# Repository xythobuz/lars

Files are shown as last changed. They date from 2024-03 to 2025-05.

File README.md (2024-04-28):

# LARS - Looping Automated Rhythm Station






This is a simple drum machine / loopstation.
It's made for three hand-wound solenoids mounted to a tambourine.
It is controlled by a Raspberry Pi Pico on a custom PCB.

Please take a look at [the auto-generated documentation](https://xythobuz.github.io/lars/).

Also see [this blog post for some more context](https://www.xythobuz.de/lars.html).

## Quick Start

Initialize your local repo and prepare the build:

    git clone https://git.xythobuz.de/thomas/drumkit.git
    cd drumkit
    git submodule update --init
    cd pico-sdk
    git submodule update --init
    cd ..
    mkdir build
    cd build
    cmake ..
    cd ..

Then you can build new binaries like this:

    make -Cbuild -j4

For the first time, flash as usual using the mass storage bootloader (hold BOOTSEL while pluggin in the Pico).
After the firmware has been flashed once you can just use the included `flash.sh` to avoid having to hold the button.
Use `debug.sh` to open a serial console via USB.

## Documentation

You can find the [documentation here on GitHub pages](https://xythobuz.github.io/lars/).

The docs are built using [mdbook](https://github.com/rust-lang/mdBook), licensed as `MPL-2.0`.
Get the [latest release from GitHub](https://github.com/rust-lang/mdBook/releases) for a pre-built binary if you want to test changes to the docs locally.

    ./pcb/generate_plot.sh
    ./pcb2/generate_plot.sh
    ./3dprint/generate_stls.sh

    ./docs/generate_docs.sh serve

This will open your browser to a local development instance of the docs.

## Hardware Connections

These are the used pins on the first prototype.
Follow these if you want to build your own version without the included PCB design.

    Pin 1    GP0    I2C0 SDA
    Pin 2    GP1    I2C0 SCL

    Pin 29   GP22   Output Channel A
    Pin 31   GP26   Output Channel B
    Pin 32   GP27   Output Channel C

    Pin 34   GP28   Vbat (ADC2)

    Pin 11   GP8    Button 1
    Pin 12   GP9    Button 2
    Pin 16   GP12   Button 3
    Pin 19   GP14   Button 4

    Pin 22   GP17   Encoder A
    Pin 24   GP18   Encoder B
    Pin 21   GP16   Encoder Click

    Pin 14   GP10   LED 1
    Pin 15   GP11   LED 2
    Pin 17   GP13   LED 3
    Pin 20   GP15   LED 4

## License

The firmware of this project is licensed as GPLv3.
A copy of the license can be found in `COPYING`.

It uses the [Pi Pico SDK](https://github.com/raspberrypi/pico-sdk), licensed as BSD 3-clause, and therefore also [TinyUSB](https://github.com/hathach/tinyusb), licensed under the MIT license.

Some code is adapted from the TinyUSB examples.

To control the OLED display, [pico-ssd1306](https://github.com/daschr/pico-ssd1306) is used, licensed under the MIT license.

The code in `src/encoder.c` is derived from [mathertel/RotaryEncoder](https://github.com/mathertel/RotaryEncoder) and therefore licensed as BSD 3-clause.

Repo metadata is embedded into the project using [cmake-git-version-tracking](https://github.com/andrew-hardin/cmake-git-version-tracking), licensed under the MIT license.

The docs are built using [mdbook](https://github.com/rust-lang/mdBook), licensed as `MPL-2.0`.

The PCB SVG files in the documentation are displayed using [svg-pan-zoom](https://github.com/bumbu/svg-pan-zoom), licensed as `BSD-2-Clause`.

The 3D PCB files in the documentation are displayed using [three.js](hhttps://github.com/mrdoob/three.js), licensed as `MIT`.

Some code in `docs/src/js/3d.js` is derived from [a blog post of Michal Jirků](https://wejn.org/2020/12/cracking-the-threejs-object-fitting-nut/).

    This program is free software: you can redistribute it and/or modify
    it under the terms of the GNU General Public License as published by
    the Free Software Foundation, either version 3 of the License, or
    (at your option) any later version.

    This program is distributed in the hope that it will be useful,
    but WITHOUT ANY WARRANTY; without even the implied warranty of
    MERCHANTABILITY or FITNESS FOR A PARTICULAR PURPOSE.  See the
    GNU General Public License for more details.

    See <http://www.gnu.org/licenses/>.

The schematic and PCB design of this project is licensed under the [CERN Open Hardware Licence Version 2 - Strongly Reciprocal (CERN-OHL-S-2.0+)](https://ohwr.org/cern_ohl_s_v2.txt) or any later version.
A copy of the license can be found in `LICENSE`.

The PCB designs use a [KiCad-RP-Pico based](https://github.com/ncarandini/KiCad-RP-Pico) symbol and footprint library, licensed as `CC-BY-SA 4.0`.

The `pcb2/extern/EC12E-200.STEP` 3D model for the rotary encoder comes directly from the manufacturer, [ALPS](https://tech.alpsalpine.com/e/products/detail/EC12E24204A8/).

The `pcb2/extern/OLED_128x64.stp` 3D model for the SSD1306 OLED display is made by [
Adrián San José Torices](https://grabcad.com/library/pantalla-oled-0-96-128x64-1).

The SSD1306 footprint for pcb2 is from [KiCAD Rookie](https://kicadrookie.blogspot.com/2022/06/ssd1306-i2c-096in-oled-display-kicad_86.html).

The `pcb2/extern/5236AB/5236ab-41x408.stp` 3D model for the power switch comes directly from the manufacturer, [APEM](https://www.apem.com/idec-apem/de/Schalter-f%C3%BCr-Frontplatten/5000M/p/5236AB).

     ------------------------------------------------------------------------------
    | This source describes Open Hardware and is licensed under the CERN-OHL-S v2  |
    | or any later version.                                                        |
    |                                                                              |
    | You may redistribute and modify this source and make products using it under |
    | the terms of the CERN-OHL-S v2 (https://ohwr.org/cern_ohl_s_v2.txt)          |
    | or any later version.                                                        |
    |                                                                              |
    | This source is distributed WITHOUT ANY EXPRESS OR IMPLIED WARRANTY,          |
    | INCLUDING OF MERCHANTABILITY, SATISFACTORY QUALITY AND FITNESS FOR A         |
    | PARTICULAR PURPOSE. Please see the CERN-OHL-S v2 (or any later version)      |
    | for applicable conditions.                                                   |
    |                                                                              |
    | Source location: https://git.xythobuz.de/thomas/drumkit                      |
    |                                                                              |
    | As per CERN-OHL-S v2 section 4, should You produce hardware based on this    |
    | source, You must where practicable maintain the Source Location visible      |
    | on the external case of the Gizmo or other products you make using this      |
    | source.                                                                      |
     ------------------------------------------------------------------------------

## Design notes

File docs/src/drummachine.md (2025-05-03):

# Drum Machine

The drum-machine runs through a sequence of a given length, set by the `Length` menu.

The corresponding LED lights up at it's moment in the sequence.
The currently active "step" is fully bright while enabled ones are lit dimly.

Change the speed the sequence is running at with the `BPM` setting.

If you have selected a `Length` that is longer than the available number of buttons / LEDs, you can switch your "window" of the sequence using the `Bank` setting.

Select the currently edited output channel with the `Channel` menu.

Use the CLEAR button below the encoder to zero-out the currently selected channel.

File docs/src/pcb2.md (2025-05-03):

# LARS V2

This is the second iteration of the hardware.
The principle is the same as for the prototype, with the same chinese modules used.
Only the buttons have been changed, and there are now 9 of them, with 8 LEDs.
The battery is now mounted on the board.
It is planned to be used without a case.

You can [download the Gerber files to order PCBs online](./plot/fab_pcb2.zip).

assembled V2 PCB (https://www.xythobuz.de/img/lars_v2_1.jpg)

Revision 1 was using the SMD-only footprint for the Raspberry Pi Pico.
Revision 2 has changed this to be compatible to THT as well.

**Warning:**
Revision 1 and 2 are missing diodes on the button matrix.
So when holding down three or more buttons simultaneously you get ghosting on other buttons.

Depending on the solenoids you may reach a situation where not all channels can be properly triggered simultaneously.

**To Do**: try to improve this by adding more capacitance to the power rail or between the voltage regulators and the mosfets?

## Bill of Materials

These are all the parts required to assemble the V2 PCB.

| ID | Type | Link |
| -- | ---- | ---- |
| U1 | Raspberry Pi Pico | [Reichelt.de](https://www.reichelt.de/raspberry-pi-pico-rp2040-cortex-m0-microusb-rasp-pi-pico-p295706.html?&nbc=1), [Amazon.de](https://www.amazon.de/Raspberry-Pi-Pico/dp/B09KVB8LVR) |
| U2 | TP4056 Charger Module | [Amazon.de](https://www.amazon.de/AZDelivery-%E2%AD%90%E2%AD%90%E2%AD%90%E2%AD%90%E2%AD%90-TP4056-Laderegler-Lithium/dp/B07D2G345P) |
| U3 - U5 | MOSFET Module N-Channel | [Amazon.de](https://www.amazon.de/Schaltersteuerplatine-Motorsteuerplatine-MOSFET-Triggerschalter-Reglersteuerplatine-Dual-Hochleistungs/dp/B0CBK7D1GD) |
| U6 - U8 | Step-Up Converter Module | [Amazon.de](https://www.amazon.de/Converter-Spannungswandler-LAOMAO-Netzteil-Kompatibel/dp/B0B932BR7V) |
| OLED1 | SSD1306 128x64 0.96" Display | [Amazon.de](https://www.amazon.de/AZDelivery-Display-Arduino-Raspberry-gratis/dp/B01L9GC470) |
| BT1 | Keystone 1042 | [Reichelt.de](https://www.reichelt.de/batteriehalter-fuer-1-18650-keystone-1042-p213369.html?&nbc=1) |
| S1 | APEM 5236AB | [Reichelt.de](https://www.reichelt.de/kippschalter-1a-250vac-1x-ein-ein-printanschluss-as-500apc-p4396.html?&nbc=1) |
| SW1 | ALPS EC12E24244 | [Reichelt.de](https://www.reichelt.de/drehimpulsegeber-24-impulse-24-rastungen-vertikal-stec12e08-p73923.html?&nbc=1) |
| - | Cap for encoder knob | [Reichelt.de](https://www.reichelt.de/potentiometerknopf-fuer-achse-6-4-5-mm-schwarz-knopf-10-150e-p73960.html) |
| SW2 - SW10 | DIP 6x6mm push button | [Reichelt.de](https://www.reichelt.de/kurzhubtaster-printmontage-1-schliesser-6-x-6-x-5-mm-dip-dts-62k-v-p360043.html?&nbc=1) |
| D1 - D4 | 1N5819 Schottky Diode | [Reichelt.de](https://www.reichelt.de/schottkydiode-40-v-1-a-do-41-1n-5819-p41850.html?&nbc=1) |
| D5 - D12 | LED 5mm | [Reichelt.de](https://www.reichelt.de/led-5mm-bedrahtet-rot-450-mcd-90--5603r1c-khb-a-p361958.html?&nbc=1) |
| R1 | Resistor 10k Ohm 0.1% Axial | [Reichelt.de](https://www.reichelt.de/widerstand-metallschicht-10-kohm-0207-0-6-w-0-1--mpr-10-0k-p12770.html?&nbc=1) |
| R2 | Resistor 18k Ohm 0.1% Axial | [Reichelt.de](https://www.reichelt.de/widerstand-metallfilm-18-kohm-0-1-0-6-w-tk25-0207-mpr-18-0k-p12837.html?&nbc=1) |
| R3 - R10 | Resistor 1k Ohm | [Reichelt.de](https://www.reichelt.de/widerstand-metallschicht-1-00-kohm-0207-0-6-w-1--metall-1-00k-p11403.html?&nbc=1) |

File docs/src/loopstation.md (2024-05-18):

# Loop Station

LARS Loop Station controls (https://www.xythobuz.de/img/lars_loop_controls.jpg)

In this mode the first three buttons play each corresponding output channel.

The fourth (and eighth) button, with the LED always lit, is the record button.
Hold it down for a while and release it to set the length of the loop.

Notes played while the record button is held will be looped.

The fifth, sixth and seventh buttons are channel mute buttons.
While holding these down the corresponding channel will not play any notes.

The top-right button below the encoder clears the recorded loop in different ways:

 * Pressing it on its own will clear all channels of the current loop, keeping the set length.
 * Pressing it while holding down one of the channel mute buttons will clear only this channel in the current loop.
 * Pressing it while holding down the left REC button will clear the current loop, including the length.
 * Pressing it while holding down the right REC button will clear all loops in all banks.

You can modify the loop length using the encoder menu.

The encoder menu also provides a way to switch between different loop banks.
With the `Sel-Bnk` menu you can switch to another loop bank.
With the `Cpy-Bnk` menu you can copy the current loop to another bank and switch to it.

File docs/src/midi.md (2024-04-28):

# MIDI

The MIDI mode is only available when a computer is connected via USB to the Raspberry Pi Pico.

You only have two settings in this mode, the receive and transmit MIDI channels, ranging from 1 to 16.

Notes received on the selected Rx channel will be played on the output channels.
Velocity is ignored.

Any pressed note buttons are sent on the selected Tx channel.

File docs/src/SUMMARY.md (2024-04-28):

# Summary

# LARS

- [Introduction](./introduction.md)

# Electronics

- [Prototype](./pcb1.md)
  - [Schematics](./pcb1_sch.md)
  - [PCB Layout](./pcb1_pcb.md)
- [LARS V2](./pcb2.md)
  - [Schematics](./pcb2_sch.md)
  - [PCB Layout](./pcb2_pcb.md)

# 3D Printed Parts

- [Solenoids](./3dprint_solenoids.md)
- [Tambourine](./3dprint_tambourine.md)
- [Prototype](./3dprint_prototype.md)

# Firmware

- [Usage Guide](./usage.md)
  - [Loop Station](./loopstation.md)
  - [Drum Machine](./drummachine.md)
  - [MIDI](./midi.md)

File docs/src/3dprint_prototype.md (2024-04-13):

# 3D Print - Prototype

This page shows the 3D printed parts for the prototype PCB.

The dimensions for the parametric OpenSCAD settings for these generated STL files should match what we used for the prototype.
For your own build you may need to get the OpenSCAD sources [from the repo](https://github.com/xythobuz/lars/tree/master/3dprint) and tweak the values.

## Enclosure Bottom

{{#include inc_enclosure_bottom.stl.md}}

[Direct link to this file](./stl/enclosure_bottom.stl).

## Enclosure Top

{{#include inc_enclosure_top.stl.md}}

[Direct link to this file](./stl/enclosure_top.stl).

## Enclosure Faceplate

{{#include inc_enclosure_faceplate.stl.md}}

[Direct link to this file](./stl/enclosure_faceplate.stl).

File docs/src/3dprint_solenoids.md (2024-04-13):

# 3D Print - Solenoids

This page shows the 3D printed parts for the solenoid actuators.

The dimensions for the parametric OpenSCAD settings for these generated STL files should match what we used for the prototype.
For your own build you may need to get the OpenSCAD sources [from the repo](https://github.com/xythobuz/lars/tree/master/3dprint) and tweak the values.

## Actuator All

{{#include inc_actuator_all.stl.md}}

[Direct link to this file](./stl/actuator_all.stl).

## Actuator Cap

{{#include inc_actuator_cap.stl.md}}

[Direct link to this file](./stl/actuator_cap.stl).

## Actuator Hammer

{{#include inc_actuator_hammer.stl.md}}

[Direct link to this file](./stl/actuator_hammer.stl).

## Actuator Spool

{{#include inc_actuator_spool.stl.md}}

[Direct link to this file](./stl/actuator_spool.stl).

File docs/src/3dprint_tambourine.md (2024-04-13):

# 3D Print - Tambourine

This page shows the 3D printed parts to mount solenoids to a tambourine.

The dimensions for the parametric OpenSCAD settings for these generated STL files should match what we used for the prototype.
For your own build you may need to get the OpenSCAD sources [from the repo](https://github.com/xythobuz/lars/tree/master/3dprint) and tweak the values.

## Beam

{{#include inc_beam_all.stl.md}}

[Direct link to this file](./stl/beam_all.stl).

## Tamb Mount All Visualize

{{#include inc_tamb_mount_all_visualize.stl.md}}

[Direct link to this file](./stl/tamb_mount_all_visualize.stl).

## Tamb Mount Inner

{{#include inc_tamb_mount_inner.stl.md}}

[Direct link to this file](./stl/tamb_mount_inner.stl).

## Tamb Mount Outer

{{#include inc_tamb_mount_outer.stl.md}}

[Direct link to this file](./stl/tamb_mount_outer.stl).

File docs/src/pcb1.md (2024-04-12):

# Prototype

This is the hardware design for the initial prototype gifted as a birthday present.
It's a single sided PCB layout suitable for hand etching at home.

hand etching prototype pcb (https://www.xythobuz.de/img/lars_13.jpg)
assembled prototype (https://www.xythobuz.de/img/lars_10.jpg)

You can also [download the Gerber files to order PCBs online](./plot/fab_pcb.zip).

## Bill of Materials

These are all the parts required to assemble the prototype.

| ID | Type | Link |
| -- | ---- | ---- |
| U9 | Raspberry Pi Pico | [Reichelt.de](https://www.reichelt.de/raspberry-pi-pico-rp2040-cortex-m0-microusb-rasp-pi-pico-p295706.html?&nbc=1), [Amazon.de](https://www.amazon.de/Raspberry-Pi-Pico/dp/B09KVB8LVR) |
| U2 | TP4056 Charger Module | [Amazon.de](https://www.amazon.de/AZDelivery-%E2%AD%90%E2%AD%90%E2%AD%90%E2%AD%90%E2%AD%90-TP4056-Laderegler-Lithium/dp/B07D2G345P) |
| U4, U6, U8 | MOSFET Module N-Channel | [Amazon.de](https://www.amazon.de/Schaltersteuerplatine-Motorsteuerplatine-MOSFET-Triggerschalter-Reglersteuerplatine-Dual-Hochleistungs/dp/B0CBK7D1GD) |
| U3, U5, U7 | Step-Up Converter Module | [Amazon.de](https://www.amazon.de/Converter-Spannungswandler-LAOMAO-Netzteil-Kompatibel/dp/B0B932BR7V) |
| J2 | SSD1306 128x64 0.96" Display | [Amazon.de](https://www.amazon.de/AZDelivery-Display-Arduino-Raspberry-gratis/dp/B01L9GC470) |
| S1 | ALPS EC12E24244 | [Reichelt.de](https://www.reichelt.de/drehimpulsegeber-24-impulse-24-rastungen-vertikal-stec12e08-p73923.html?&nbc=1) |
| - | Cap for encoder knob | [Reichelt.de](https://www.reichelt.de/potentiometerknopf-fuer-achse-6-4-5-mm-schwarz-knopf-10-150e-p73960.html) |
| D1 - D4 | LED 5mm | [Reichelt.de](https://www.reichelt.de/led-5mm-bedrahtet-rot-450-mcd-90--5603r1c-khb-a-p361958.html?&nbc=1) |
| D5 - D8 | 1N5819 Schottky Diode | [Reichelt.de](https://www.reichelt.de/schottkydiode-40-v-1-a-do-41-1n-5819-p41850.html?&nbc=1) |
| R1 - R4 | Resistor 1k Ohm | [Reichelt.de](https://www.reichelt.de/widerstand-metallschicht-1-00-kohm-0207-0-6-w-1--metall-1-00k-p11403.html?&nbc=1) |
| R5 | Resistor 10k Ohm 0.1% Axial | [Reichelt.de](https://www.reichelt.de/widerstand-metallschicht-10-kohm-0207-0-6-w-0-1--mpr-10-0k-p12770.html?&nbc=1) |
| R6 | Resistor 18k Ohm 0.1% Axial | [Reichelt.de](https://www.reichelt.de/widerstand-metallfilm-18-kohm-0-1-0-6-w-tk25-0207-mpr-18-0k-p12837.html?&nbc=1) |
| SW1 - SW4 | 12mm waterproof stainless steel push button | N/A |
| SW5A | Unknown Power Switch | N/A |

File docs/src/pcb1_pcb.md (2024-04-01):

# Prototype PCB Layout

This page shows the current version of the PCB layout as SVG graphics.

You can [download the Gerber files to order PCBs online](./plot/fab_pcb.zip).

## 2D PCB Layout

You can also view the [2D PCB layout as PDF](./plot/drumkit.kicad_pcb.pdf).

<script src="js/svg-pan-zoom.js" charset="UTF-8"></script>
<div style="background-color: white; border: 1px solid black;">
    <embed type="image/svg+xml" src="./plot/drumkit.kicad_pcb.svg" id="pz_drumkit0" style="width: 100%;"/>
    <script>
        document.getElementById('pz_drumkit0').addEventListener('load', function(){
            svgPanZoom(document.getElementById('pz_drumkit0'), {controlIconsEnabled: true, minZoom: 1.0});
        })
    </script>
</div>

[Direct link to this file](./plot/drumkit.kicad_pcb.svg).

## DIY Version

The DIY version is suitable for etching at home, it only needs the bottom copper layer.
Be aware that there is one track on the top layer, for a safety diode that was added later.
This connection should be done with a wire by hand.

You can also view the [DIY layout as PDF](./plot/drumkit.kicad_pcb_diy.pdf).

<script src="js/svg-pan-zoom.js" charset="UTF-8"></script>
<div style="background-color: white; border: 1px solid black;">
    <embed type="image/svg+xml" src="./plot/drumkit.kicad_pcb_diy.svg" id="pz_drumkit1" style="width: 100%;"/>
    <script>
        document.getElementById('pz_drumkit1').addEventListener('load', function(){
            svgPanZoom(document.getElementById('pz_drumkit1'), {controlIconsEnabled: true, minZoom: 1.0});
        })
    </script>
</div>

[Direct link to this file](./plot/drumkit.kicad_pcb_diy.svg).

## 3D PCB Layout

{{#include inc_drumkit.kicad_pcb.md}}

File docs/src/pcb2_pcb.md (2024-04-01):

# LARS V2 PCB Layout

This page shows the current version of the PCB layout as SVG graphics.

You can [download the Gerber files to order PCBs online](./plot/fab_pcb2.zip).

## 2D PCB Layout

You can also view the [2D PCB layout as PDF](./plot/lars2.kicad_pcb.pdf).

<script src="js/svg-pan-zoom.js" charset="UTF-8"></script>
<div style="background-color: white; border: 1px solid black;">
    <embed type="image/svg+xml" src="./plot/lars2.kicad_pcb.svg" id="pz_drumkit0" style="width: 100%;"/>
    <script>
        document.getElementById('pz_drumkit0').addEventListener('load', function(){
            svgPanZoom(document.getElementById('pz_drumkit0'), {controlIconsEnabled: true, minZoom: 1.0});
        })
    </script>
</div>

[Direct link to this file](./plot/lars2.kicad_pcb.svg).

## 3D PCB Layout

{{#include inc_lars2.kicad_pcb.md}}

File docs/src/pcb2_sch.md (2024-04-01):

# LARS V2 Schematics

This page shows the current version of the schematics as SVG graphics.

You can also view the [schematics as PDF](./plot/lars2.kicad_sch.pdf).

{{#include inc_lars2.kicad_sch.md}}

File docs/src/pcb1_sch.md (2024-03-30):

# Prototype Schematics

This page shows the current version of the schematics as SVG graphics.

You can also view the [schematics as PDF](./plot/drumkit.kicad_sch.pdf).

{{#include inc_drumkit.kicad_sch.md}}

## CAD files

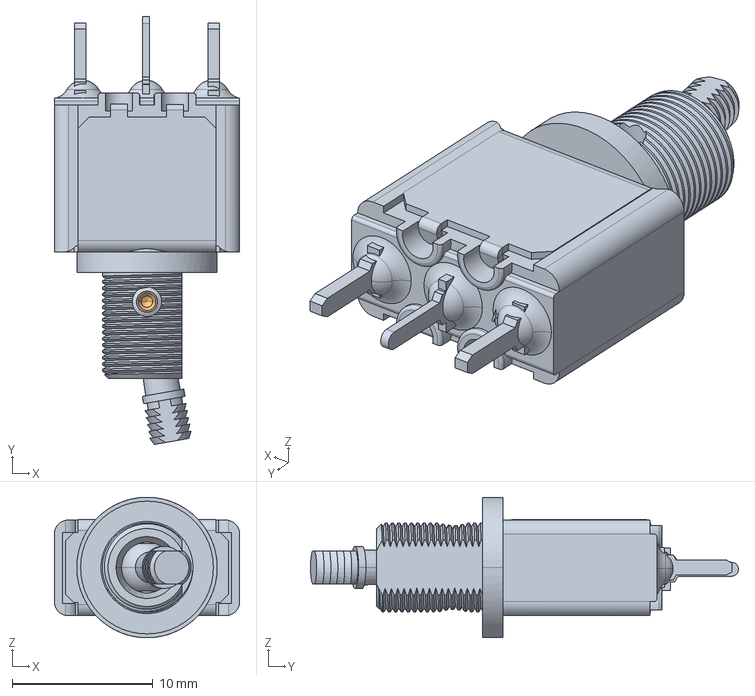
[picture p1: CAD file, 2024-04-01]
pcb2/extern/5236AB/5236ab-41x408.stp
13.2 x 30.5 x 10.0 mm

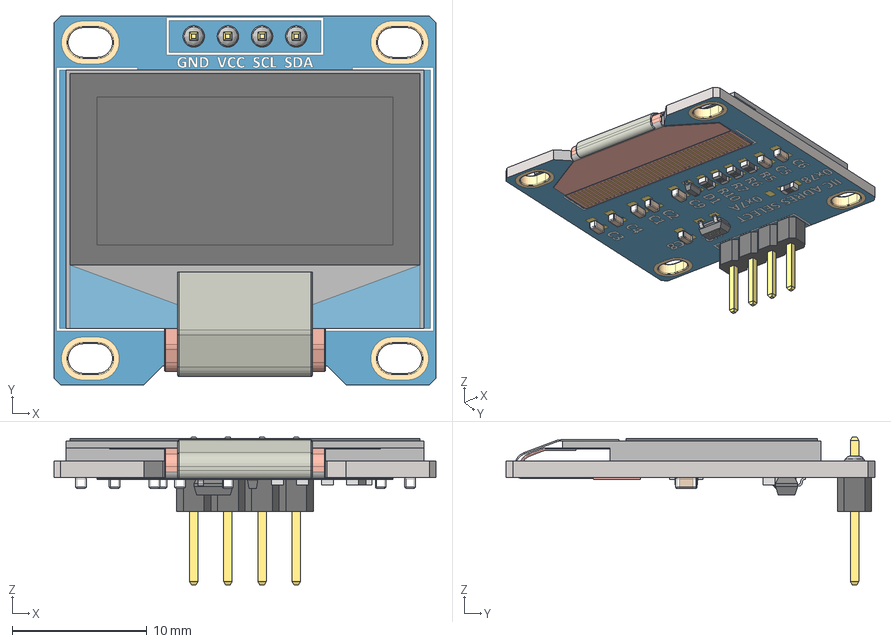
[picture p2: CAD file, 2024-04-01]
pcb2/extern/OLED_128x64.stp
28.4 x 27.4 x 11.0 mm
SOT-23_TOR
RES_CR16_MTK_1 x 4
RES_CR16_MTK
SOD323F_DIO

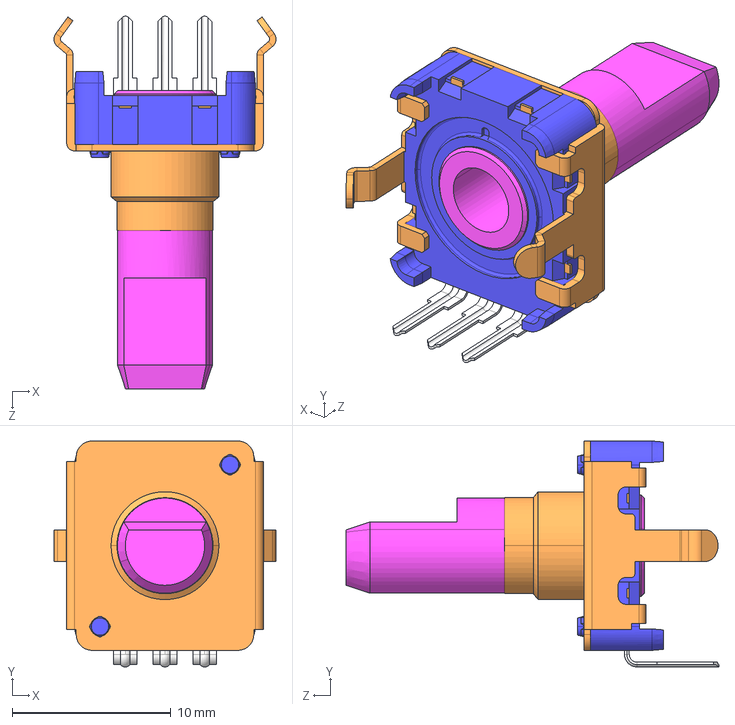
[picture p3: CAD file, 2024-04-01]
pcb2/extern/EC12E-200.STEP
14.0 x 14.2 x 23.5 mm

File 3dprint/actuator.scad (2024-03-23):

$fa=1/1;
$fs=1/2;
bissl=1/2;
part="spool";//[spool,cap,hammer,all]
total_length=50;
wall=0.8;
air=0.5;
copper_height=5;
thick_wall=2*wall; //can be specified
iron_d=4;
iron_h=total_length/3; //can be changed, but this seems optimal
spool_h=iron_h; //according to theory, optimum is a little more
iron_travel=iron_h; //may be smaller with heavy beaters or returning springs
extra_hold=iron_h/3;
spool_id=iron_d+2*air;
spool_od=spool_id+2*wall;
cap_od=spool_od+2*copper_height;
slit=15;
hole=3;
hammer_flat=true;
module spool() {
  difference() {
    union() {
      cylinder(d1=spool_od,d2=cap_od,h=thick_wall+iron_travel);
      translate([0,0,iron_travel+thick_wall]) cylinder(d=spool_od,h=spool_h+extra_hold);
    }
    translate([0,0,thick_wall]) cylinder(d=spool_id,h=spool_h+iron_h+bissl+extra_hold);
  }
}
module cap() {
difference() {
union() {
cylinder(d=cap_od,h=thick_wall);
translate([0,0,thick_wall])cylinder(d=spool_od+2*wall+2*air,h=extra_hold);
translate([-cap_od/2,0,0])cube([cap_od,cap_od/2,thick_wall]);
translate([-cap_od/2,cap_od/2,0])cube([cap_od,thick_wall,2*thick_wall+slit]);
translate([-thick_wall/2,0,0])cube([thick_wall,cap_od/2,extra_hold+thick_wall]);
}
translate([0,0,-bissl])cylinder(d=spool_id,h=extra_hold+thick_wall+2*bissl);
cylinder(d=spool_od+2*air,h=extra_hold);
hull() {
translate([cap_od/2-thick_wall-hole/2,cap_od/2+thick_wall/2,2*thick_wall+hole/2])rotate([90,0,0])cylinder (d=hole, h=thick_wall+bissl,center=true);
translate([cap_od/2-thick_wall-hole/2,cap_od/2+thick_wall/2,slit])rotate([90,0,0])cylinder (d=hole, h=thick_wall+bissl,center=true);
}
hull() {
translate([-cap_od/2+thick_wall+hole/2,cap_od/2+thick_wall/2,2*thick_wall+hole/2])rotate([90,0,0])cylinder (d=hole, h=thick_wall+bissl,center=true);
translate([-cap_od/2+thick_wall+hole/2,cap_od/2+thick_wall/2,slit])rotate([90,0,0])cylinder (d=hole, h=thick_wall+bissl,center=true);
}
}
}
echo (cap_od-thick_wall*2-hole);
module hammer() {
if (hammer_flat) {
cylinder(d=cap_od-2*air,h=thick_wall);
translate([0,0,thick_wall]) cylinder(d1=cap_od-2*air,d2=iron_d,h=cap_od/2-iron_d/2-air/2);
}
else {
cylinder(d2=cap_od/2,d1=iron_d,h=cap_od/4-iron_d/4);
translate([0,0,cap_od/4-iron_d/4])cylinder(d=cap_od/2,h=thick_wall);
translate([0,0,cap_od/4-iron_d/4+thick_wall]) cylinder(d1=cap_od/2,d2=iron_d,h=cap_od/4-iron_d/4);
}
translate([0,0,thick_wall+cap_od/2-iron_d/2-air/2]) cylinder(d=iron_d,h=1.5*iron_h);
}
if (part=="all") {
spool();
translate([0,0,spool_h+iron_h+bissl+air+thick_wall])cap();
translate([0,0,total_length])mirror([0,0,1])hammer();
}
if (part=="spool") spool();
if (part=="cap") cap();
if (part=="hammer") hammer();

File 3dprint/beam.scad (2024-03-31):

part="all";//[all]
$fa=1/1;
$fs=1/2;
bissl=1/100;
wall=1.6;//twice nozzle diameter is fine, walls of triangles
hole=3; //hole for mounting thread inserts
hd=10; //horizontal distance between mounting points, depends on mounting hole distance in the actuator
height=40; //dimension of the beam in the direction of tambourine depth
vd=height-wall; //vertical distance between mounting holes
segments=14; //number of mounting points, defines the beam length
radius=1; //rounding of inner corners
thickness=2*wall+hole; //thickness of the beam, keep some material to properly hold the threaded insert on the side
offset=wall/2+hole/2;
difference() {
  linear_extrude(thickness, convexity=4) difference() {
    offset(r=-radius)offset(r=radius)union() {
      for (i=[0:hd:hd*(segments-1)]) translate ([i,0]) {
        for (tr=[[[hd,0],[0,0]],[[-hd/2,vd],[0,0]],[[hd/2,vd],[0,0]],[[hd/2,vd],[-hd/2,vd]]]) hull() { //diagonals
          translate(tr[0])circle(d=wall);
          translate(tr[1]) circle(d=wall);
        }
        for (tr=[[hd/2,vd-offset],[-hd/2,vd-offset],[hd,offset],[0,offset]]) translate(tr)circle(d=2*wall+hole); //big circles
      }
    
      //left vertical wall, not generated by the loop
      for (tr=[[[-hd/2-offset,0],[0,0]],[[-hd/2-offset,0],[-hd/2-offset,vd]],[[-hd/2-offset,vd],[-hd/2,vd]]]) hull() {
        translate(tr[0])circle(d=wall);
        translate(tr[1]) circle(d=wall);
      }

      //solid triangle to jhold threaded inserts
      hull() for (tr=[[0,0],[-hd/2-offset,0],[-hd/2-offset,vd],[-hd/2,vd]]) translate(tr) circle(d=wall); 

      //right vertical wall, not generated by the loop
      for (tr=[[[hd*segments+offset,0],[0,0]],
               [[hd*segments+offset,0],[hd*segments+offset,vd]],
               [[hd*segments+offset,vd],[hd*(segments-0.5),vd]],
               [[hd*segments,0],[hd*(segments-0.5),vd]]]) 
        hull() {
          translate(tr[0])circle(d=wall);
          translate(tr[1]) circle(d=wall);
        }
    }
    for (i=[0:segments]) {
      translate([i*hd,offset]) circle(d=hole);
      translate([(i-0.5)*hd,vd-offset]) circle(d=hole);
    }
  }
  //mounting holes for threaded inserts, three just in case, it's better to use the middle one
  translate([-hd/2-offset-wall/2,height/4-wall,thickness/2])rotate([0,90,0])cylinder(d=hole,h=hd-wall);
  translate([-hd/2-offset-wall/2,height/2-wall/2,thickness/2])rotate([0,90,0])cylinder(d=hole,h=hd-wall);
  translate([-hd/2-offset-wall/2,height*3/4,thickness/2])rotate([0,90,0])cylinder(d=hole,h=hd-wall);
}

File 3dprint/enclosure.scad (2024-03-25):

//currantly the box is unfinished, but you can still use faceplate.
$fa=1/1;
$fs=1/2;
bissl=1/100;
part="bottom";//[bottom,top,faceplate]
pegs_h=5;
pegs_id=3;
pegs_od=7;
wall=1;
depth=30;
air=0.5; //wiggle room
//board (and box) size goes here
//defined as corners of inner space relatove to x=y=0 point on the board
//[x1,y1,x2,y2]
board=[-2,-2,90.81+4,118.75+2];
screen=[67.2+2,16.5-10,20,27];
//holes in the front panel
//defined as [x,y,diameter], where x from KiCAD becomes y and y becomes x, because
//coordinate conventions in Kicad and OpenSCAD are mirrored
holes_positions=[
  [48.90,66.68,12], //encoder
  [48.3,85.4,7], //power
  [71.12,48.26,8], //leds
  [71.12,67.31,8],
  [71.12,86.36,8],
  [71.12,105.41,8],
  [85.73,48,12], //buttons
  [85.73,67.3,12],
  [85.73,86.36,12],
  [85.73,105.41,12]];
//standoffs to hold the board
//defined as [x,y,id,od,height], where x from KiCAD becomes y and y becomes x, because
//coordinate conventions in Kicad and OpenSCAD are mirrored
mount_pegs=[
  [1.90,1.90,pegs_id,pegs_od,pegs_h],
  [1.90,116.84,pegs_id,pegs_od,pegs_h],
  [88.90,1.90,pegs_id,pegs_od,pegs_h],
  [88.90,116.84,pegs_id,pegs_od,pegs_h]
];
module bottom() {
  difference() {
    translate([board[0]-wall,board[1]-wall,-wall]) cube([board[2]-board[0]+2*wall,board[3]-board[1]+2*wall,depth+wall]);
    translate([board[0],board[1],0]) cube([board[2]-board[0],board[3]-board[1],depth+bissl]);
  }
  for (peg=mount_pegs) {
    translate([peg[0],peg[1],0]) difference() {
      cylinder(d=peg[3],h=peg[4]);
      translate([0,0,-bissl]) cylinder(d=peg[2],h=peg[4]+2*bissl);
    }
  }
}
module faceplate() {
  difference() {
    translate([board[0]-wall,board[1]-wall,0]) cube([board[2]-board[0]+2*wall,board[3]-board[1]+2*wall,wall]);
    for (hole=holes_positions) {
      translate([hole[0],hole[1],-bissl]) cylinder(d=hole[2],h=wall+2*bissl);
    }
    translate([screen[0],screen[1],-bissl])cube([screen[2],screen[3],wall+2*bissl]);
  }
};
module top() {
  mirror([0,0,1])faceplate();
    difference() {
    translate([board[0]-wall,board[1]-wall,0]) cube([board[2]-board[0]+2*wall,board[3]-board[1]+2*wall,depth]);
    translate([board[0],board[1],-bissl]) cube([board[2]-board[0],board[3]-board[1],depth+2*bissl]);
  }
}
if (part=="bottom") bottom();
if (part=="faceplate") faceplate();
if (part=="top") top();
if (part=="all") {
  bottom();
  translate([0,0,depth+wall]) faceplate();
}

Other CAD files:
3dprint/tamb_mount.scad

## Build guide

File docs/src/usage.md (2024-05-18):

# Usage Guide

Turn on LARS using the power switch on the PCB.

In normal operation, the bottom of the display always shows the battery level in percent, and the voltage.
Take care to **turn off the device** and recharge it when the **percentage reaches zero**!

The top of the screen shows the currently selected setting and its value.
Press the encoder to switch to the next available setting, or turn the encoder to change the value of the currently selected setting.

The available settings depend on the current mode.
Take a look at the sub-page for each mode for details.

You can hold down some buttons while powering on the device to get different effects:

* hold the `Clear` button to enter the configuration menu
* hold the encoder `Click` button to show version information of the firmware
* hold both `Clear` and `Click` to enter the button test mode
* hold any combination of three buttons to skip the boot animation

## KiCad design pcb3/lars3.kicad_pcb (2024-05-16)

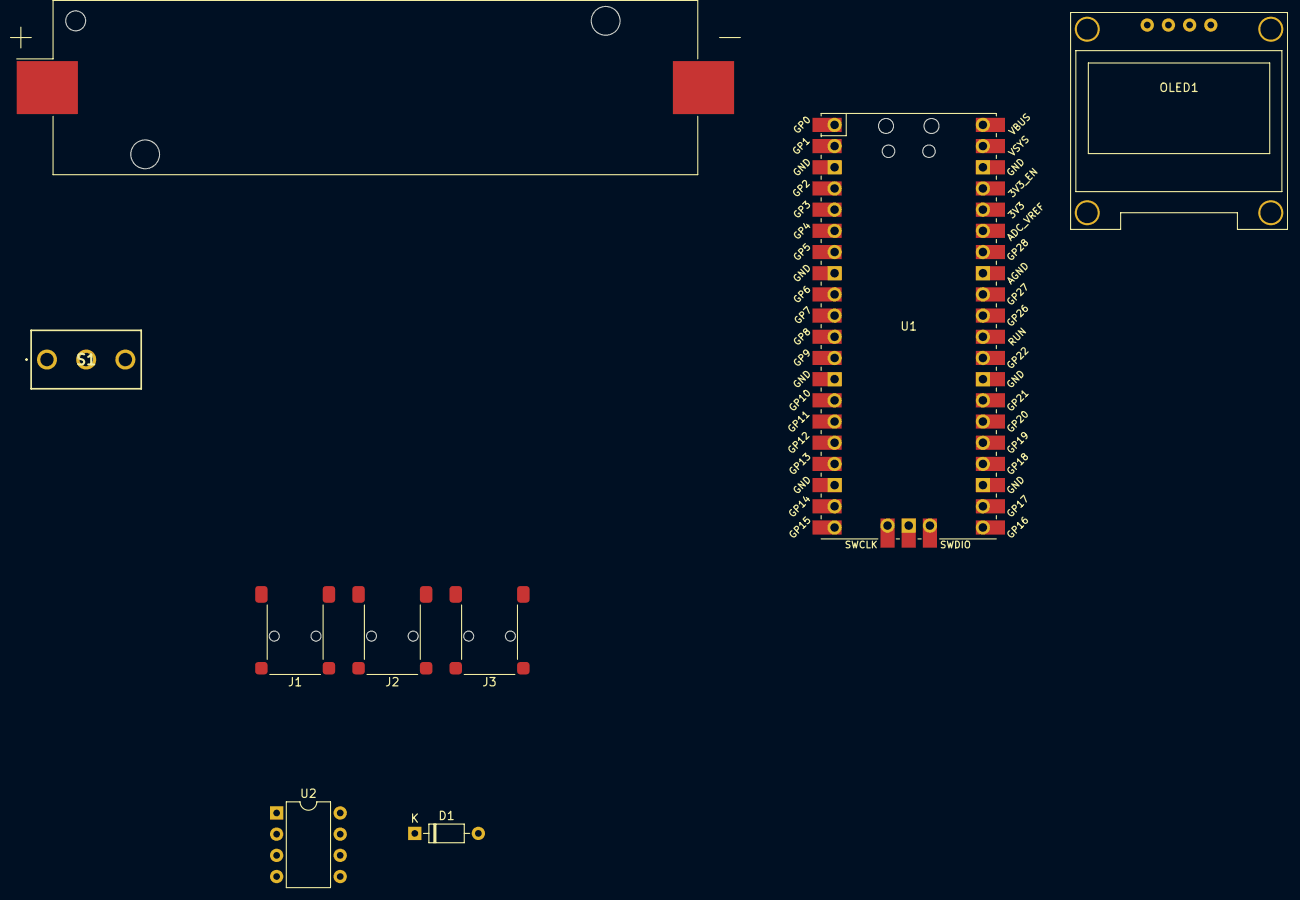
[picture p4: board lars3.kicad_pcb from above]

Board: 2 copper layers, 9 parts (0 on the bottom side), 3 nets, no tracks yet.

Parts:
BT1: Battery_Cell; BatteryHolder_Keystone_1042_1x18650
D1: 1N914; D_DO-35_SOD27_P7.62mm_Horizontal
J1: MIDI IN; Jack_3.5mm_Lumberg_1503_02_Horizontal
J2: MIDI OUT; Jack_3.5mm_Lumberg_1503_02_Horizontal
J3: MIDI THRU; Jack_3.5mm_Lumberg_1503_02_Horizontal
OLED1: SSD1306; SSD1306_0.96_Oled
S1: 5236AB
U1: Pico; RPi_Pico_SMD_TH
U2: 6N138; DIP-8_W7.62mm

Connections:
GND: J2.S, J3.S, U2.5 (GND)
unnamed: D1.2 (A), J1.T, U2.3 (C2)
unnamed: D1.1 (K), U2.2 (C1)

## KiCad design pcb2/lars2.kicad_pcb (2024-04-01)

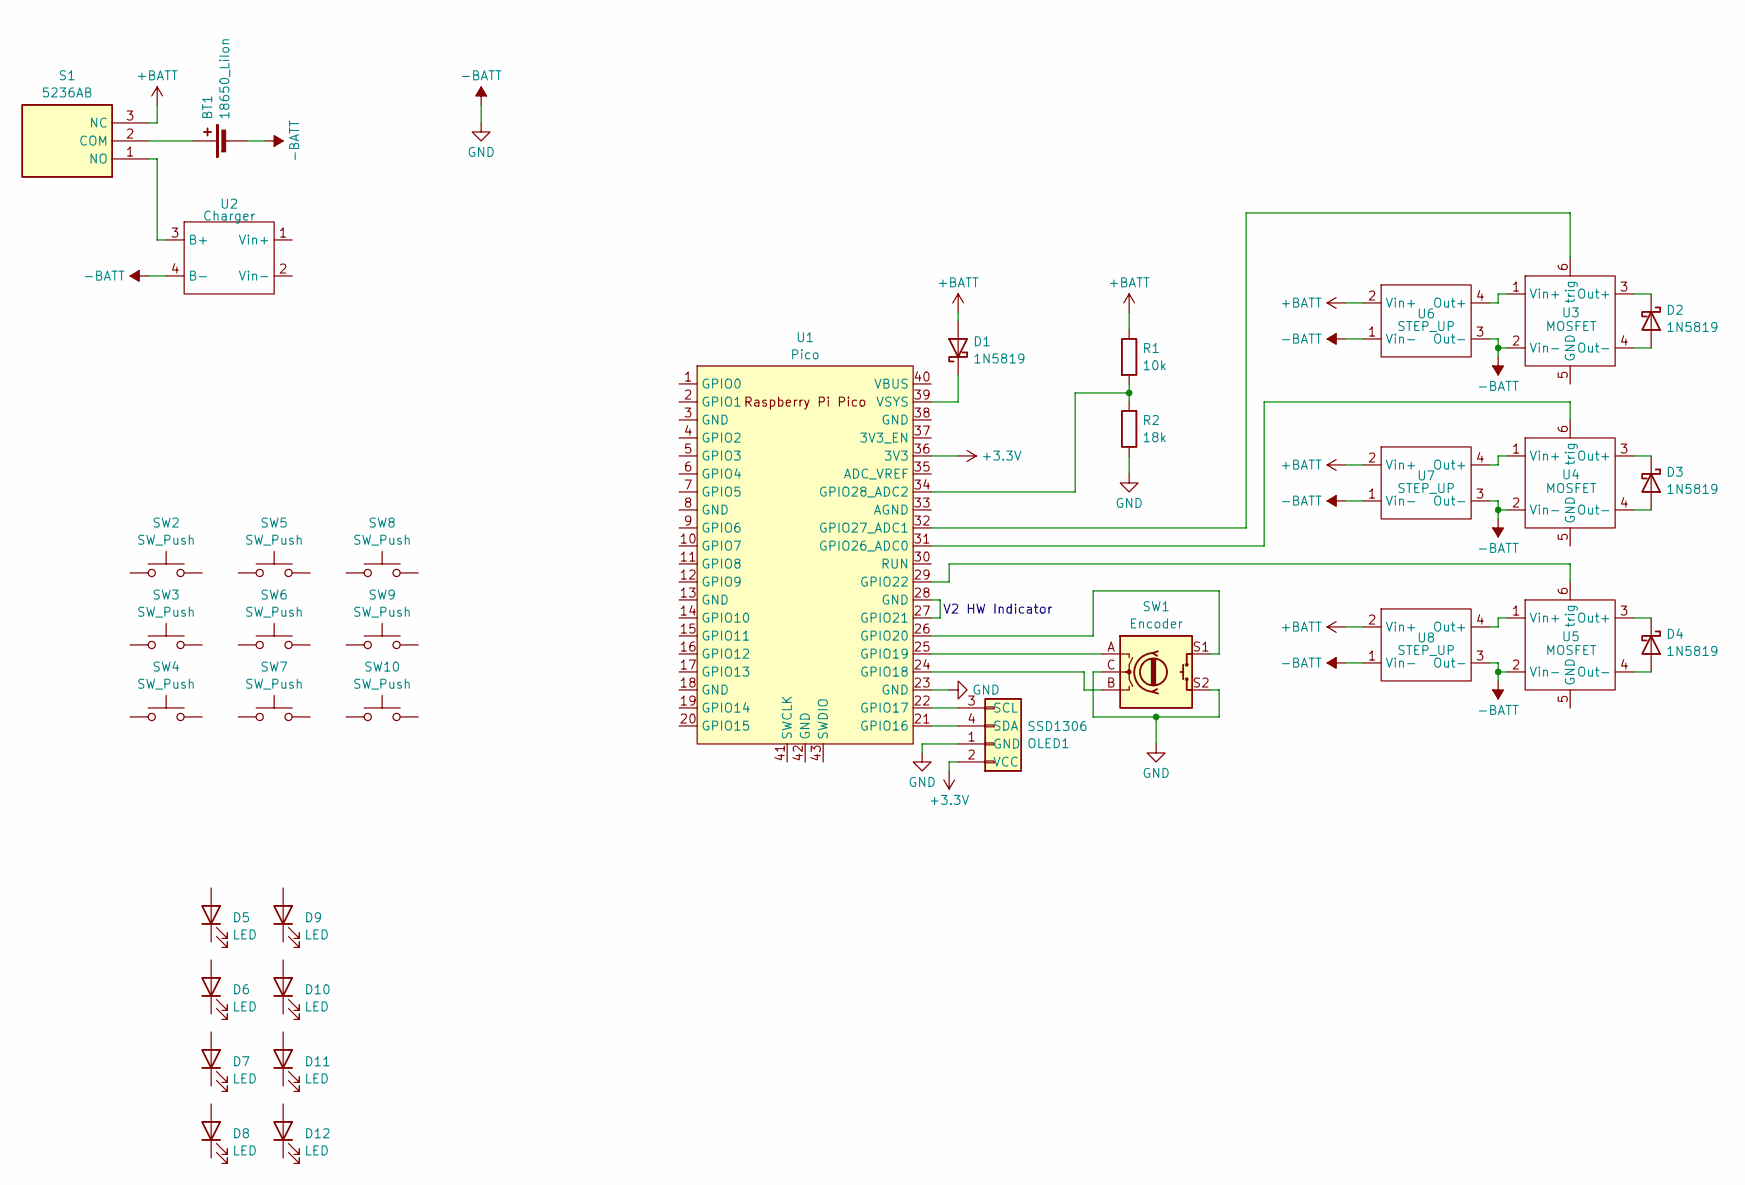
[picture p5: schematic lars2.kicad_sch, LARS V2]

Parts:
BT1: 18650_LiIon; BatteryHolder_Keystone_1042_1x18650
D1, D2, D3, D4: 1N5819; D_DO-41_SOD81_P10.16mm_Horizontal
D5, D6, D7, D8, D9, D10, D11, D12: LED; LED_D5.0mm
OLED1: SSD1306; SSD1306_0.96_Oled
R1: 10k; R_Axial_DIN0204_L3.6mm_D1.6mm_P2.54mm_Vertical
R2: 18k; R_Axial_DIN0204_L3.6mm_D1.6mm_P2.54mm_Vertical
S1: 5236AB; Manufacturer_Part_Number 5236AB
SW1: Encoder; RotaryEncoder_Alps_EC12E-Switch_Vertical_H20mm_CircularMoun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
SW2, SW3, SW4, SW5, SW6, SW7, SW8, SW9, SW10: SW_Push; SW_PUSH_6mm_H5mm
U1: Pico; RPi_Pico_SMD_only
U2: Charger; charger
U3, U4, U5: MOSFET; xy-mos
U6, U7, U8: STEP_UP; dc-dc module

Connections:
+3.3V: OLED1.2 (VCC), U1.36 (3V3)
+BATT: D1.2 (A), R1.1, S1.3 (NC), U6.2 (Vin+), U7.2 (Vin+), U8.2 (Vin+)
-BATT: BT1.2 (-), OLED1.1 (GND), R2.1, SW1.C, SW1.S2, U1.23 (GND), U2.4 (B-), U3.2 (Vin-), U4.2 (Vin-), U5.2 (Vin-), U6.1 (Vin-), U6.3 (Out-), U7.1 (Vin-), U7.3 (Out-), U8.1 (Vin-), U8.3 (Out-)
unnamed: BT1.1 (+), S1.2 (COM)
unnamed: D1.1 (K), U1.39 (VSYS)
unnamed: D2.2 (A), U3.4 (Out-)
unnamed: D2.1 (K), U3.3 (Out+)
unnamed: D3.2 (A), U4.4 (Out-)
unnamed: D3.1 (K), U4.3 (Out+)
unnamed: D4.2 (A), U5.4 (Out-)
unnamed: D4.1 (K), U5.3 (Out+)
unnamed: OLED1.3 (SCL), U1.22 (GPIO17)
unnamed: OLED1.4 (SDA), U1.21 (GPIO16)
unnamed: S1.1 (NO), U2.3 (B+)
unnamed: SW1.B, U1.24 (GPIO18)
unnamed: SW1.A, U1.25 (GPIO19)
unnamed: SW1.S1, U1.26 (GPIO20)
unnamed: U1.27 (GPIO21), U1.28 (GND)
unnamed: U1.29 (GPIO22), U5.6 (trig)
unnamed: U1.31 (GPIO26_ADC0), U4.6 (trig)
unnamed: U1.32 (GPIO27_ADC1), U3.6 (trig)
unnamed: R1.2, R2.2, U1.34 (GPIO28_ADC2)
unnamed: U3.1 (Vin+), U6.4 (Out+)
unnamed: U4.1 (Vin+), U7.4 (Out+)
unnamed: U5.1 (Vin+), U8.4 (Out+)

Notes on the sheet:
V2 HW Indicator

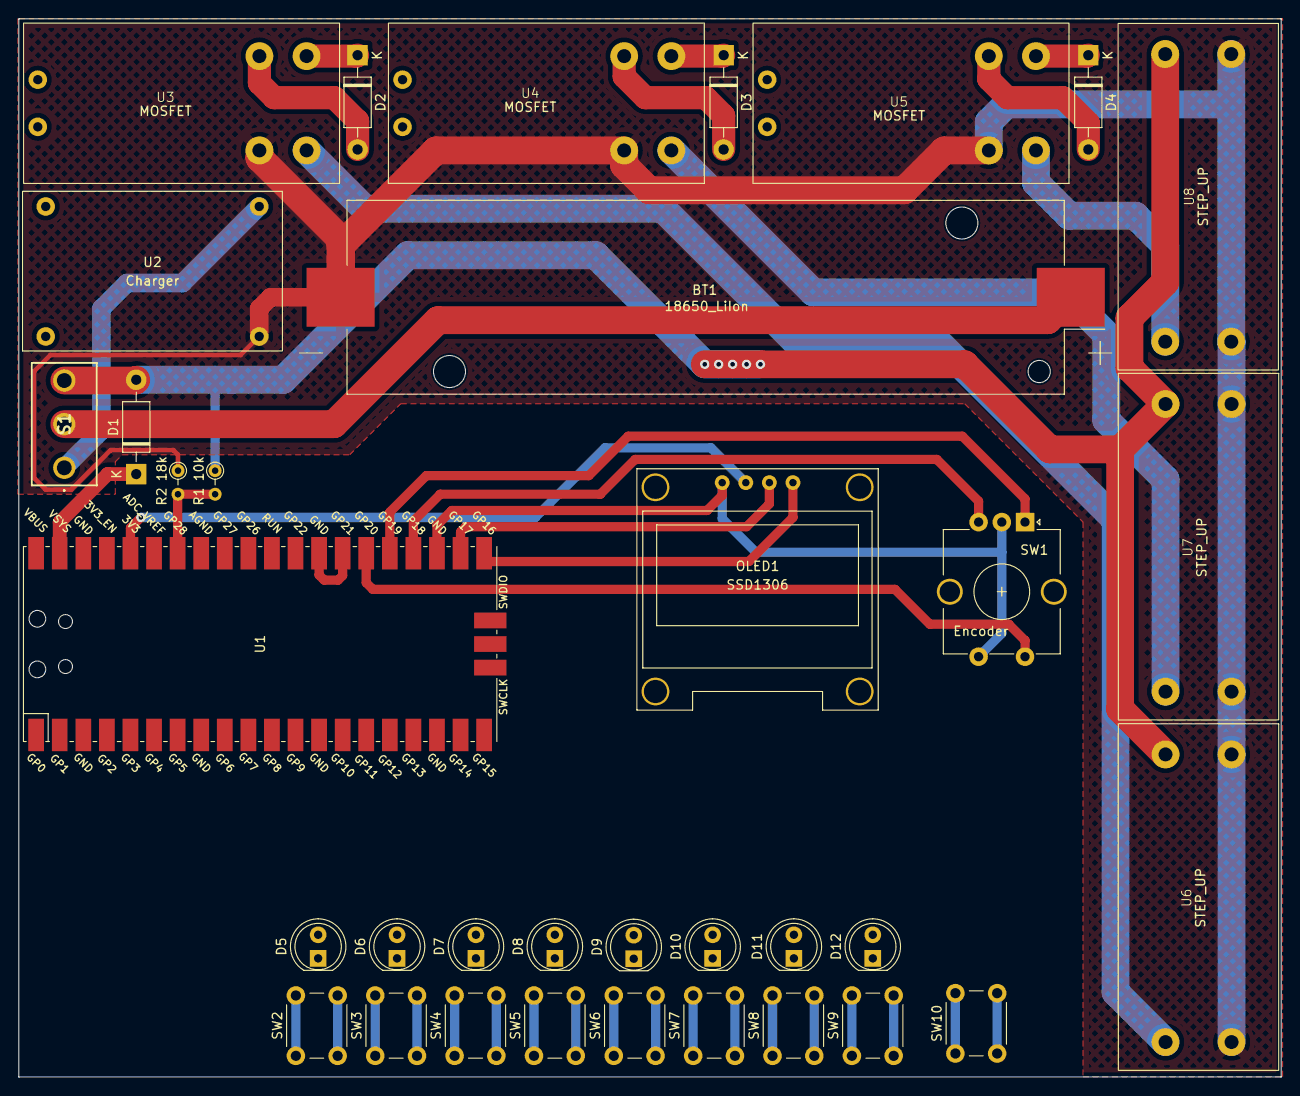
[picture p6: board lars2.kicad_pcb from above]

Board: 2 copper layers, 136.0 x 114.0 mm, 35 parts (0 on the bottom side), 25 nets.

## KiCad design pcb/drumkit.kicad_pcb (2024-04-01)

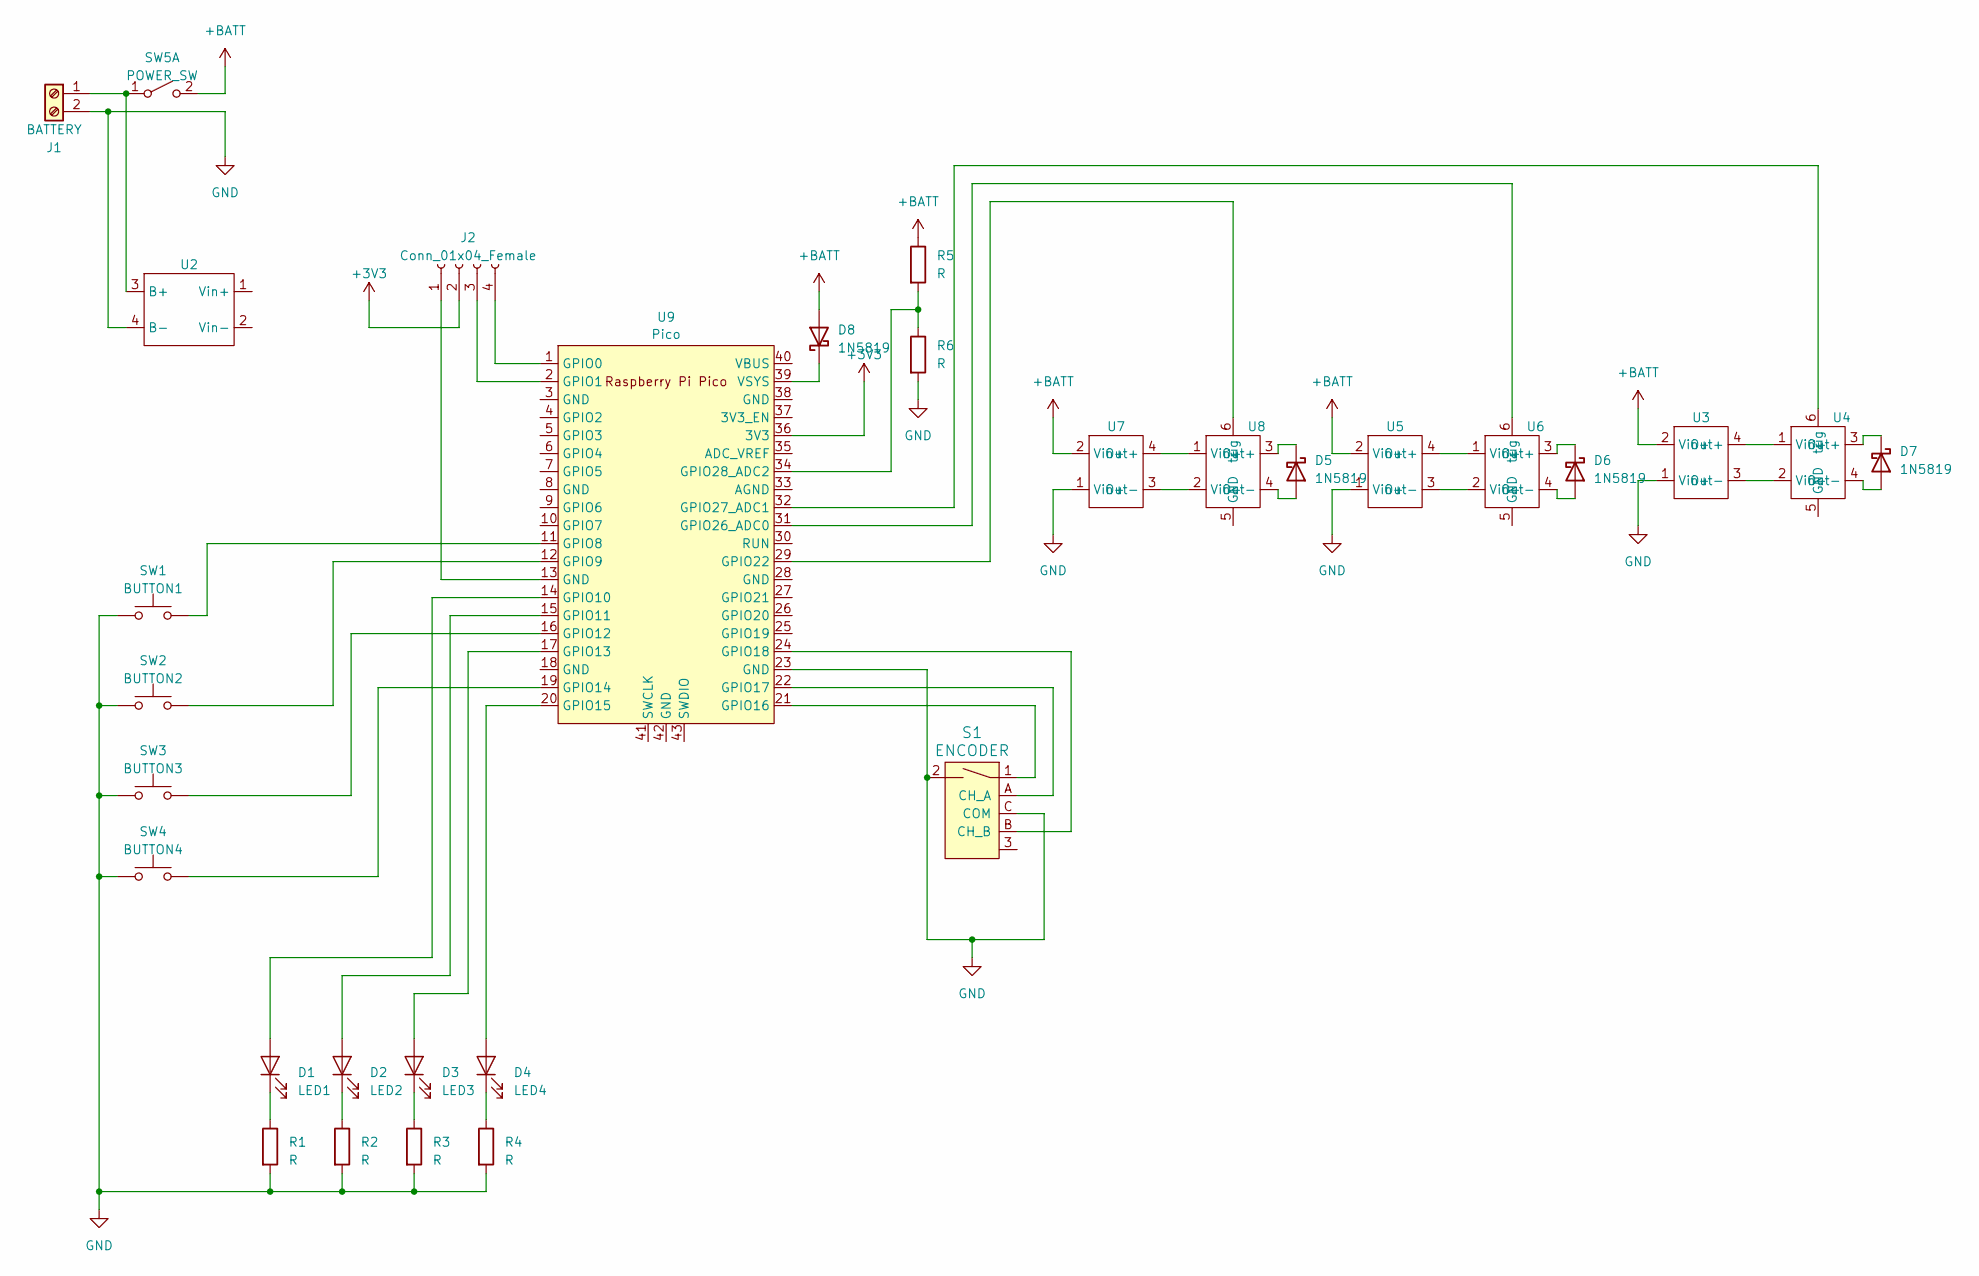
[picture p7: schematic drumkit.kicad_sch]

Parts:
D1: LED1; LED_D5.0mm
D2: LED2; LED_D5.0mm
D3: LED3; LED_D5.0mm
D4: LED4; LED_D5.0mm
D5, D6, D7, D8: 1N5819; D_DO-41_SOD81_P10.16mm_Horizontal
J1: BATTERY; TerminalBlock_bornier-2_P5.08mm
J2: Conn_01x04_Female; PinHeader_1x04_P2.54mm_Vertical
R1, R2, R3, R4: R; R_Axial_DIN0617_L17.0mm_D6.0mm_P5.08mm_Vertical
R5, R6: R; R_Axial_DIN0309_L9.0mm_D3.2mm_P12.70mm_Horizontal
S1: ENCODER; Rotary_Encoder_Switched_PEC11R; MPN PEC11R-4215F-S0024; Digi-Key_PN PEC11R-4215F-S0024-ND
SW1: BUTTON1; L_Radial_D12.0mm_P6.00mm_MuRATA_1900R
SW2: BUTTON2; L_Radial_D12.0mm_P6.00mm_MuRATA_1900R
SW3: BUTTON3; L_Radial_D12.0mm_P6.00mm_MuRATA_1900R
SW4: BUTTON4; L_Radial_D12.0mm_P6.00mm_MuRATA_1900R
SW5: POWER_SW; L_Radial_D12.0mm_P6.00mm_MuRATA_1900R
U2: charger
U3, U5, U7: dc-dc module
U4, U6, U8: xy-mos
U9: Pico; RPi_Pico_SMD_TH_noSWD

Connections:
+3V3: J2.2, U9.36 (3V3)
+BATT: D8.2 (A), R5.1, SW5.2 (B), U3.2 (Vin+), U5.2 (Vin+), U7.2 (Vin+)
GND: J1.2, R1.2, R2.2, R3.2, R4.2, R6.2, S1.2, S1.C (COM), SW1.1, SW2.1, SW3.1, SW4.1, U2.4 (B-), U3.1 (Vin+), U5.1 (Vin+), U7.1 (Vin+), U9.23 (GND)
unnamed: D1.2 (A), U9.14 (GPIO10)
unnamed: D1.1 (K), R1.1
unnamed: D2.2 (A), U9.15 (GPIO11)
unnamed: D2.1 (K), R2.1
unnamed: D3.2 (A), U9.17 (GPIO13)
unnamed: D3.1 (K), R3.1
unnamed: D4.2 (A), U9.20 (GPIO15)
unnamed: D4.1 (K), R4.1
unnamed: D5.2 (A), U8.4 (Out-)
unnamed: D5.1 (K), U8.3 (Out+)
unnamed: D6.2 (A), U6.4 (Out-)
unnamed: D6.1 (K), U6.3 (Out+)
unnamed: D7.2 (A), U4.4 (Out-)
unnamed: D7.1 (K), U4.3 (Out+)
unnamed: D8.1 (K), U9.39 (VSYS)
unnamed: J1.1, SW5.1 (A), U2.3 (B+)
unnamed: J2.1, U9.13 (GND)
unnamed: J2.3, U9.2 (GPIO1)
unnamed: J2.4, U9.1 (GPIO0)
unnamed: S1.A (CH_A), U9.22 (GPIO17)
unnamed: S1.B (CH_B), U9.24 (GPIO18)
unnamed: U3.4 (Out+), U4.1 (Vin+)
unnamed: U3.3 (Out-), U4.2 (Vin-)
unnamed: U4.6 (trig), U9.32 (GPIO27_ADC1)
unnamed: U5.4 (Out+), U6.1 (Vin+)
unnamed: U5.3 (Out-), U6.2 (Vin-)
unnamed: U6.6 (trig), U9.31 (GPIO26_ADC0)
unnamed: U7.4 (Out+), U8.1 (Vin+)
unnamed: U7.3 (Out-), U8.2 (Vin-)
unnamed: U8.6 (trig), U9.29 (GPIO22)
unnamed: SW1.2, U9.11 (GPIO8)
unnamed: SW2.2, U9.12 (GPIO9)
unnamed: SW3.2, U9.16 (GPIO12)
unnamed: SW4.2, U9.19 (GPIO14)
unnamed: S1.1, U9.21 (GPIO16)
unnamed: R5.2, R6.1, U9.34 (GPIO28_ADC2)

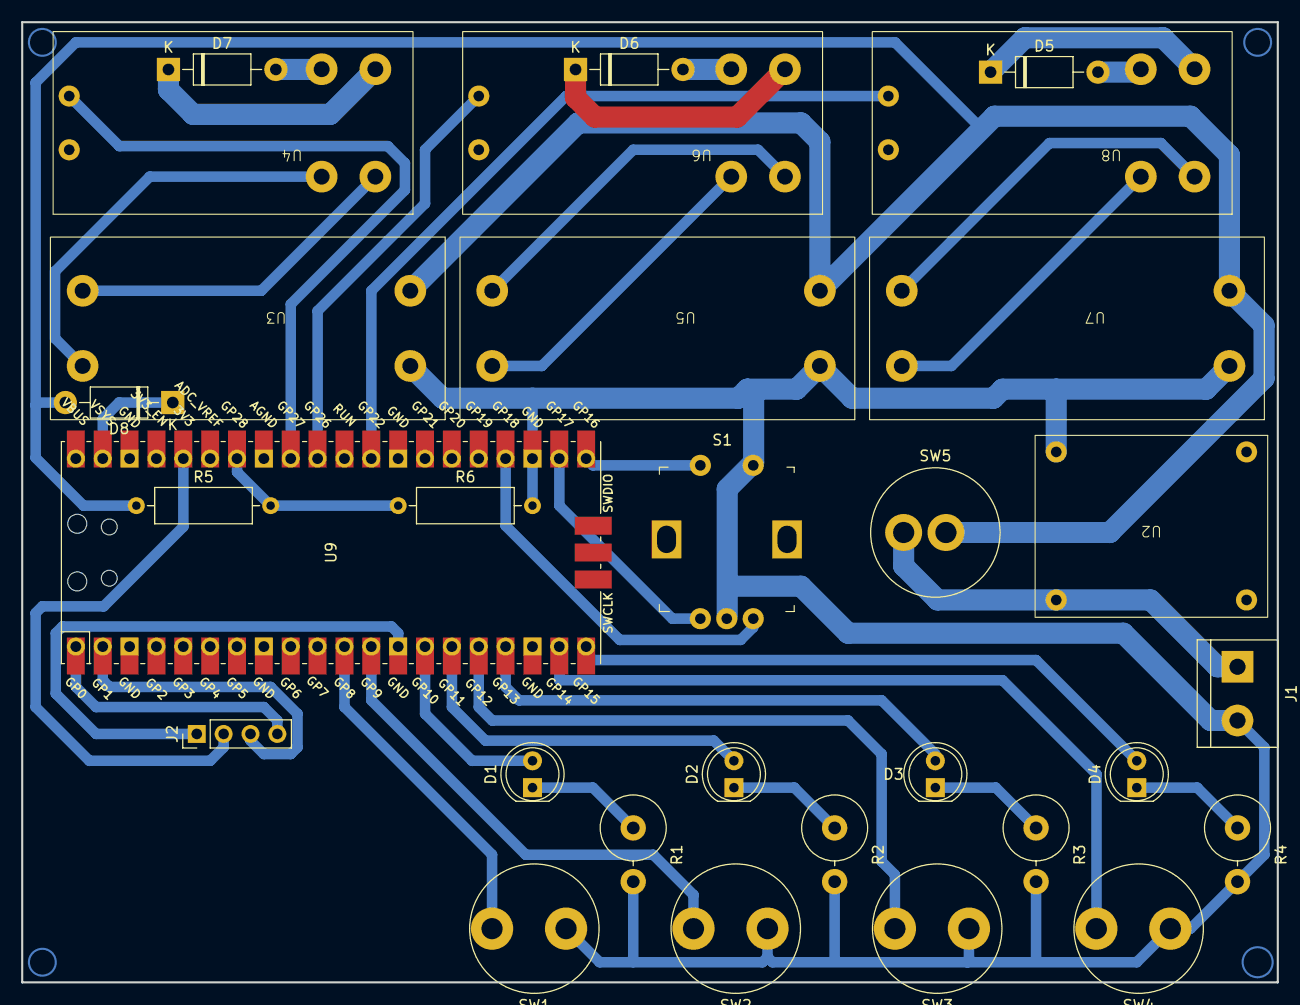
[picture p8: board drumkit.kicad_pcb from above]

Board: 2 copper layers, 118.7 x 90.8 mm, 30 parts (0 on the bottom side), 39 nets.

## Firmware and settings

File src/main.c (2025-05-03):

/*
 * main.c
 *
 * Copyright (c) 2024 Thomas Buck (thomas@xythobuz.de)
 *
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
 * See <http://www.gnu.org/licenses/>.
 */

#include "pico/stdlib.h"
#include "pico/bootrom.h"
#include "hardware/watchdog.h"

#include "config.h"
#include "adc.h"
#include "buttons.h"
#include "console.h"
#include "encoder.h"
#include "lcd.h"
#include "led.h"
#include "log.h"
#include "logo.h"
#include "mem.h"
#include "pulse.h"
#include "sequence.h"
#include "settings.h"
#include "ui.h"
#include "usb.h"
#include "main.h"

static const uint gpio_hw_detect = 21;

enum hw_versions hw_type = HW_UNKNOWN;

static bool debug_buttons[NUM_BTNS] = {0};

static void debug_buttons_callback(enum buttons btn, bool v) {
    debug_buttons[btn] = v;
}

static uint32_t debug_count_buttons(void) {
    uint32_t cnt = 0;
    for (uint32_t i = 0; i < NUM_BTNS; i++) {
        if (debug_buttons[i]) {
            cnt++;
        }
    }
    return cnt;
}

void reset_to_bootloader(void) {
    lcd_draw_bye();

#ifdef PICO_DEFAULT_LED_PIN
    reset_usb_boot(1 << PICO_DEFAULT_LED_PIN, 0);
#else // ! PICO_DEFAULT_LED_PIN
    reset_usb_boot(0, 0);
#endif // PICO_DEFAULT_LED_PIN
}

void reset_to_main(void) {
    watchdog_enable(1, 0);
    while (1);
}

static void sleep_ms_wd(uint32_t ms) {
    for (uint32_t i = 0; i < ms; i++) {
        watchdog_update();
        sleep_ms(1);
    }
}

static void hw_type_detection(void) {
    gpio_init(gpio_hw_detect);
    gpio_set_dir(gpio_hw_detect, GPIO_IN);
    gpio_pull_up(gpio_hw_detect);

    if (gpio_get(gpio_hw_detect)) {
        hw_type = HW_PROTOTYPE;
    } else {
        hw_type = HW_V2;
    }
}

static void animate_boot_combos(void) {
    // read out button state for debug options
    buttons_callback(debug_buttons_callback);
    for (uint i = 0; i < (DEBOUNCE_DELAY_MS + 5); i++) {
        watchdog_update();
        buttons_run();
        usb_run();
        cnsl_run();
        sleep_ms_wd(1);
    }

    uint32_t cnt = debug_count_buttons();

    // handle special button combos on boot
    if ((cnt == 2) && debug_buttons[BTN_CLEAR] && debug_buttons[BTN_CLICK]) {
        lcd_debug_buttons();
    } else if ((cnt == 1) && debug_buttons[BTN_CLEAR]) {
        // enter settings menu
        settings_init();
        settings_run();
        sleep_ms_wd(mem_data()->boot_anim_ms);
    } else if (cnt == 3) {
        // skip splash screen
    } else if ((cnt == 1) && debug_buttons[BTN_CLICK]) {
        // show version info
        lcd_draw_version();

        // wait until button is released
        uint32_t last = to_ms_since_boot(get_absolute_time());
        bool state = false;
        while (debug_buttons[BTN_CLICK]) {
            watchdog_update();
            buttons_run();
            usb_run();
            cnsl_run();
            uint32_t now = to_ms_since_boot(get_absolute_time());
            if ((now - last) >= 250) {
                state = !state;
                last = now;
                led_set(0, state);
            }
        }
        led_set(0, false);
    } else {
        // show splash for a bit and animate LEDs
        for (uint i = 0; i < led_count(); i++) {
            watchdog_update();
            usb_run();
            cnsl_run();
            led_set(i, true);
            sleep_ms_wd(mem_data()->boot_anim_ms / led_count());
        }
    }

    // turn off LEDs at end of init
    for (uint i = 0; i < led_count(); i++) {
        led_set(i, false);
    }
}

void main_loop_hw(void) {
    watchdog_update();

    usb_run();
    cnsl_run();
    buttons_run();
    encoder_run();
    sequence_run();
    pulse_run();
    ui_run();

    ui_encoder(encoder_get_diff());
}

int main(void) {
    watchdog_enable(WATCHDOG_PERIOD_MS, 1);

    cnsl_init();
    usb_init();
    mem_load();

    hw_type_detection();

    bat_init();
    buttons_init();
    encoder_init();
    lcd_init();
    led_init();

    // show logo
    lcd_draw_bitmap(logo_data,
                    LOGO_WIDTH, LOGO_HEIGHT,
                    0, 0);

    animate_boot_combos();

    sequence_init();
    ui_init();

    debug("init done\n");

    while (1) {
        main_loop_hw();
    }

    return 0;
}

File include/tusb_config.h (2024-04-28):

/*
 * Extended from TinyUSB example code.
 *
 * Copyright (c) 2022 - 2024 Thomas Buck (thomas@xythobuz.de)
 *
 * The MIT License (MIT)
 *
 * Copyright (c) 2019 Ha Thach (tinyusb.org)
 *
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
 */

#ifndef _TUSB_CONFIG_H_
#define _TUSB_CONFIG_H_

#ifdef __cplusplus
 extern "C" {
#endif

//--------------------------------------------------------------------
// COMMON CONFIGURATION
//--------------------------------------------------------------------

// defined by board.mk
#ifndef CFG_TUSB_MCU
  #error CFG_TUSB_MCU must be defined
#endif

// RHPort number used for device can be defined by board.mk, default to port 0
#ifndef BOARD_DEVICE_RHPORT_NUM
  #define BOARD_DEVICE_RHPORT_NUM     0
#endif

// RHPort max operational speed can defined by board.mk
// Default to Highspeed for MCU with internal HighSpeed PHY (can be port specific), otherwise FullSpeed
#ifndef BOARD_DEVICE_RHPORT_SPEED
  #if (CFG_TUSB_MCU == OPT_MCU_LPC18XX || CFG_TUSB_MCU == OPT_MCU_LPC43XX || CFG_TUSB_MCU == OPT_MCU_MIMXRT10XX || \
       CFG_TUSB_MCU == OPT_MCU_NUC505  || CFG_TUSB_MCU == OPT_MCU_CXD56 || CFG_TUSB_MCU == OPT_MCU_SAMX7X)
    #define BOARD_DEVICE_RHPORT_SPEED   OPT_MODE_HIGH_SPEED
  #else
    #define BOARD_DEVICE_RHPORT_SPEED   OPT_MODE_FULL_SPEED
  #endif
#endif

// Device mode with rhport and speed defined by board.mk
#if   BOARD_DEVICE_RHPORT_NUM == 0
  #define CFG_TUSB_RHPORT0_MODE     (OPT_MODE_DEVICE | BOARD_DEVICE_RHPORT_SPEED)
#elif BOARD_DEVICE_RHPORT_NUM == 1
  #define CFG_TUSB_RHPORT1_MODE     (OPT_MODE_DEVICE | BOARD_DEVICE_RHPORT_SPEED)
#else
  #error "Incorrect RHPort configuration"
#endif

#ifndef CFG_TUSB_OS
#define CFG_TUSB_OS               OPT_OS_NONE
#endif

// CFG_TUSB_DEBUG is defined by compiler in DEBUG build
// #define CFG_TUSB_DEBUG           0

/* USB DMA on some MCUs can only access a specific SRAM region with restriction on alignment.
 * Tinyusb use follows macros to declare transferring memory so that they can be put
 * into those specific section.
 * e.g
 * - CFG_TUSB_MEM SECTION : __attribute__ (( section(".usb_ram") ))
 * - CFG_TUSB_MEM_ALIGN   : __attribute__ ((aligned(4)))
 */
#ifndef CFG_TUSB_MEM_SECTION
#define CFG_TUSB_MEM_SECTION
#endif

#ifndef CFG_TUSB_MEM_ALIGN
#define CFG_TUSB_MEM_ALIGN          __attribute__ ((aligned(4)))
#endif

//--------------------------------------------------------------------
// DEVICE CONFIGURATION
//--------------------------------------------------------------------

#ifndef CFG_TUD_ENDPOINT0_SIZE
#define CFG_TUD_ENDPOINT0_SIZE    64
#endif

//------------- CLASS -------------//
#define CFG_TUD_HID               0
#define CFG_TUD_CDC               1
#define CFG_TUD_MSC               0
#define CFG_TUD_MIDI              1
#define CFG_TUD_VENDOR            0

// HID buffer size Should be sufficient to hold ID (if any) + Data
#define CFG_TUD_HID_EP_BUFSIZE    16

// CDC FIFO size of TX and RX
#define CFG_TUD_CDC_RX_BUFSIZE   (TUD_OPT_HIGH_SPEED ? 512 : 64)
#define CFG_TUD_CDC_TX_BUFSIZE   (TUD_OPT_HIGH_SPEED ? 512 : 64)

// CDC Endpoint transfer buffer size, more is faster
#define CFG_TUD_CDC_EP_BUFSIZE   (TUD_OPT_HIGH_SPEED ? 512 : 64)

// MIDI FIFO size of TX and RX
#define CFG_TUD_MIDI_RX_BUFSIZE  (TUD_OPT_HIGH_SPEED ? 512 : 64)
#define CFG_TUD_MIDI_TX_BUFSIZE  (TUD_OPT_HIGH_SPEED ? 512 : 64)

// MIDI Endpoint transfer buffer size, more is faster
#define CFG_TUD_CDC_MIDI_BUFSIZE (TUD_OPT_HIGH_SPEED ? 512 : 64)

#ifdef __cplusplus
 }
#endif

#endif /* _TUSB_CONFIG_H_ */

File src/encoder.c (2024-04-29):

/*
 * encoder.c
 *
 * Based on https://github.com/mathertel/RotaryEncoder/blob/master/src/RotaryEncoder.cpp
 *
 * Copyright (c) 2024 Thomas Buck (thomas@xythobuz.de)
 *
 * Copyright (c) by Matthias Hertel, http://www.mathertel.de
 * This work is licensed under a BSD 3-Clause style license
 * https://www.mathertel.de/License.aspx.
 */

#include <stdio.h>
#include "pico/stdlib.h"

#include "main.h"
#include "log.h"
#include "encoder.h"

#define LATCH0 0
#define LATCH3 3

#define FOUR3 1 // 4 steps, Latch at position 3 only (compatible to older versions)
#define FOUR0 2 // 4 steps, Latch at position 0 (reverse wirings)
#define TWO03 3 // 2 steps, Latch at position 0 and 3

#define ENCODER_MODE FOUR3

static const uint gpio_num_proto[2] = {
    17, 18
};

static const uint gpio_num_v2[2] = {
    19, 18
};

static const int8_t KNOBDIR[] = {
    0, -1, 1, 0,
    1, 0, 0, -1,
    -1, 0, 0, 1,
    0, 1, -1, 0
};

static int8_t oldState;
static int32_t position;
static int32_t positionExt;
static int32_t positionExtPrev;
static uint32_t positionExtTime;
static uint32_t positionExtTimePrev;

void encoder_init(void) {
    for (uint i = 0; i < 2; i++) {
        if (hw_type == HW_PROTOTYPE) {
            gpio_init(gpio_num_proto[i]);
            gpio_set_dir(gpio_num_proto[i], GPIO_IN);
            gpio_pull_up(gpio_num_proto[i]);
        } else if (hw_type == HW_V2) {
            gpio_init(gpio_num_v2[i]);
            gpio_set_dir(gpio_num_v2[i], GPIO_IN);
            gpio_pull_up(gpio_num_v2[i]);
        }
    }

    if (hw_type == HW_PROTOTYPE) {
        oldState = gpio_get(gpio_num_proto[0]) | (gpio_get(gpio_num_proto[1]) << 1);
    } else if (hw_type == HW_V2) {
        oldState = gpio_get(gpio_num_v2[0]) | (gpio_get(gpio_num_v2[1]) << 1);
    }

    position = 0;
    positionExt = 0;
    positionExtPrev = 0;
    positionExtTime = 0;
    positionExtTimePrev = 0;
}

int32_t encoder_pos(void) {
    return positionExt;
}

// TODO should be adaptive depending on value range to be changed
#define ENCODER_RPM_VALUE_FACTOR 100.0f

int32_t encoder_get_diff(void) {
    int32_t diff = positionExt - positionExtPrev;
    positionExtPrev = positionExt;

#ifdef ENCODER_RPM_VALUE_FACTOR
    if (diff != 0) {
        uint32_t rpm = encoder_get_rpm();
        float f = 1.0f + ((float)rpm / ENCODER_RPM_VALUE_FACTOR);
        //debug("diff=%"PRIi32" rpm=%"PRIu32" result=%.1f", diff, rpm, diff * f);
        return diff * f;
    }
#endif

    return diff;
}

uint32_t encoder_get_rpm(void) {
    // calculate max of difference in time between last position changes or last change and now.
    uint32_t timeBetweenLastPositions = positionExtTime - positionExtTimePrev;
    uint32_t timeToLastPosition = to_ms_since_boot(get_absolute_time()) - positionExtTime;
    uint32_t t = MAX(timeBetweenLastPositions, timeToLastPosition);
    return (60.0f * 1000.0f) / ((float)(t * 20));
}

void encoder_run(void) {
    int8_t thisState = 0;
    if (hw_type == HW_PROTOTYPE) {
        thisState = gpio_get(gpio_num_proto[0]) | (gpio_get(gpio_num_proto[1]) << 1);
    } else if (hw_type == HW_V2) {
        thisState = gpio_get(gpio_num_v2[0]) | (gpio_get(gpio_num_v2[1]) << 1);
    }

    if (oldState != thisState) {
        position += KNOBDIR[thisState | (oldState << 2)];
        oldState = thisState;

        switch (ENCODER_MODE) {
        case FOUR3:
            if (thisState == LATCH3) {
                // The hardware has 4 steps with a latch on the input state 3
                positionExt = position >> 2;
                positionExt = -positionExt;

                positionExtTimePrev = positionExtTime;
                positionExtTime = to_ms_since_boot(get_absolute_time());
            }
            break;

        case FOUR0:
            if (thisState == LATCH0) {
                // The hardware has 4 steps with a latch on the input state 0
                positionExt = position >> 2;
                positionExt = -positionExt;

                positionExtTimePrev = positionExtTime;
                positionExtTime = to_ms_since_boot(get_absolute_time());
            }
            break;

        case TWO03:
            if ((thisState == LATCH0) || (thisState == LATCH3)) {
                // The hardware has 2 steps with a latch on the input state 0 and 3
                positionExt = position >> 1;
                positionExt = -positionExt;

                positionExtTimePrev = positionExtTime;
                positionExtTime = to_ms_since_boot(get_absolute_time());
            }
            break;
        }
    }
}

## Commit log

2024-03-18 pass encoder moves to ui
2024-03-19 start creating semiproper pcb
    [drumkit.kicad_pcb, drumkit.kicad_sch]
2024-03-21 fix board
    [drumkit.kicad_pcb, drumkit.kicad_sch, tamb_mount.scad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]
2024-03-21 board ready kinda
2024-03-21 add voltage divider
    [drumkit.kicad_pcb, drumkit.kicad_sch]
2024-03-21 apdate pin assignment
2024-03-21 update pcb pdf
2024-03-21 ipdate buttons footprints
    [drumkit.kicad_pcb]
2024-03-21 fix button placement
    [drumkit.kicad_pcb]
2024-03-21 why is it not updating?
    [drumkit.kicad_pcb]
2024-03-22 cleanup and adjust pin numbers
2024-03-22 remove kicad backups from repo
2024-03-22 mounting beam
    [beam.scad, beam.stl]
2024-03-23 more 3d-printable parts
    [actuator.scad, beam.scad, enclosure.scad]
2024-03-23 cleanup, comments
    [actuator.scad, beam.scad, tamb_mount.scad]
2024-03-24 usable faceplate
    [enclosure.scad]
2024-03-24 pcb files cleanup
2024-03-25 cleanup pcb
    [drumkit.kicad_pcb, drumkit.kicad_sch]
2024-03-29 cleanup strange connection in schematic and pcb
    [drumkit.kicad_pcb, drumkit.kicad_sch]
2024-03-29 add cern license to pcb design. export diy pcb pdf.
    [drumkit.kicad_pcb, drumkit.kicad_sch]
2024-03-29 pcb under CERN license, in readme also.
2024-03-30 squeeze in safety diodes
    [drumkit.kicad_pcb, drumkit.kicad_sch]
2024-03-30 remove STLs and add workflow to generate them
    [beam.stl, tamb_mount_inner.stl, tamb_mount_outer.stl]
2024-03-31 play around with three.js and stl and vrml loading
2024-03-31 auto center objects in 3d viewer
    [beam.scad]
2024-04-01 add project for new pcb
    [lars2.kicad_pcb, lars2.kicad_sch]
2024-04-01 add 3d model to prototype pcb
    [drumkit.kicad_pcb, drumkit.kicad_sch, lars2.kicad_pcb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]
2024-04-01 add more parts to pcb2
    [EC12E-200.STEP, lars2.kicad_pcb, lars2.kicad_sch]
2024-04-01 add more parts for pcb2 and work on placement
    [lars2.kicad_pcb, lars2.kicad_sch]
2024-04-01 add ssd1306 oled to pcb2
    [OLED_128x64.stp, lars2.kicad_pcb, lars2.kicad_sch]
2024-04-01 route pcb2 converters and outputs
    [lars2.kicad_pcb]
2024-04-01 add power switch and finish output routing
    [5236ab-41x408.stp, lars2.kicad_pcb, lars2.kicad_sch]
2024-04-01 add batt- plane
    [lars2.kicad_pcb, lars2.kicad_sch]
2024-04-01 add battery voltage divider to pcb2
    [lars2.kicad_pcb, lars2.kicad_sch]
2024-04-01 add second ground plane
    [lars2.kicad_sch]
2024-04-01 finish pcb2, now with buttons and leds
    [lars2.kicad_sch]
2024-04-01 add links to gerbers in docs
2024-04-12 implement button matrix reading
2024-04-12 print bat percent
2024-04-13 split docs 3d print page
2024-04-13 wip print version
2024-04-17 more low pass filtering for battery voltage
2024-04-28 fix some ui bugs
    [buttons.c, led.c]
2024-04-29 add some basic scaling of encoder value according to turning velocity
2024-04-29 add picture of v2 pcb to docs
2024-05-14 lars2 revision 2: use tht footprint for pi pico. improve optics of schematics matrix wiring.
    [lars2.kicad_sch]
2024-05-16 start work on pcb3 midi interface
    [lars3.kicad_pcb, lars3.kicad_sch]
2025-05-03 implement missing loop station features. update pico-sdk. other small improvements. mark as release 1.0.
    [adc.c, lcd.c]
2025-05-03 fix for ubuntu missing type print macros
2025-05-03 try again to fix for ubuntu gcc
    [led.c, settings.c]
2025-05-03 add pwm led brightness control. fix led pins for prototype hardware.
    [led.c, main.c]

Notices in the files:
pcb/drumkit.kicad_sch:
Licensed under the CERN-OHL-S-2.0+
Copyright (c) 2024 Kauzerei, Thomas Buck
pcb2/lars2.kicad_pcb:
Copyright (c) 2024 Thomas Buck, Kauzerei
